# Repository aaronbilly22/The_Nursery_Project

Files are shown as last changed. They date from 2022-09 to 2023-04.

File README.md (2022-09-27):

# The Nursery Project

Developer Names: Aaron Billones, Juan Moncada, Gillian Ford, Steven Ramundi

Date of project start: September 21, 2022

The current method of preparing pots and trays to be filled with soil and populated with seeds at Sheridan Nurseries is a process with little to no automation, requiring many manual labour hours. Recently, the owners of these farms have been finding it increasingly more difficult to fill these roles with enough workers to run the operation smoothly, and meet production demands. We aim to aid in this process by designing and implementing a machine that is able to fill trays with pots and prepare them for populating with soil and seeds. This will alleviate the reliance on manual labour and improve the overall efficiency of the farm. 

The folders and files for this project are as follows:

docs - Documentation for the project\
refs - Reference material used for the project, including papers\
src - Source code\
test - Test cases\
parts - CAD/assembly and ordered parts

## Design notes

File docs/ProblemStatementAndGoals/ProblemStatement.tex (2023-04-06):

\documentclass{article}

\usepackage{tabularx}
\usepackage{booktabs}

\title{Problem Statement and Goals\\The Nursery Project}

\author{Aaron Billones, billonea\\Gillian Ford, fordg\\Juan Moncada, moncadaj\\Steven Ramundi, ramundis}

\date{September 26, 2022}

\input{../Comments}
\input{../Common}

\begin{document}

\maketitle

\begin{table}[hp]
\caption{Revision History} \label{TblRevisionHistory}
\begin{tabularx}{\textwidth}{llX}
\toprule
\textbf{Date} & \textbf{Developer(s)} & \textbf{Change}\\
\midrule
2022-09-25 & Juan Moncada,& Initial release\\&Aaron Billones,\\&Steven Ramundi,\\&Gillian Ford \\
2023-04-05 & Juan Moncada,& Updated to better reflect final product\\
\bottomrule
\end{tabularx}
\end{table}

\newpage

\section{Problem Statement}

Sheridan Nurseries is one of Canadas largest nursery opperations and is growing year by year.
In the past few years, the company has taken steps to automate their production line and streamline their operation.
A significant amount of manual labour was seen in between the delivery of skidded pots/trays and the beginning of the propagation 
assembly line. In the current state, one employee is used to recieve stacks of pots and trays from their respective skids,
populate the trays with pots, and feed the now filled trays into the assembly line where the propagation of plants into the pots begins.
This process currently requires full-time labour from at minimum one employee, if not more, to yield the required output.

\subsection{Problem}
Sheridan Nurseries currently has no automation in their process of populating their 
trays and pots thus needing significant manual labour.

\subsection{Inputs and Outputs}
\subsubsection{Physical Input}

Physical inputs will be stacks of trays and pots.
\subsubsection{Software Input}
The system will have a signal trigger to indicate if there are any trays and pots in order to carry out its operation. 
There will also be an on/off signal and safety kill switch.
\subsubsection{Physical Output}
The physical output of this project will be the trays filled with pots ready to move on to propagation.
\subsubsection{Software Output}
The systems will display a series of warnings such as load trays (when empty), load pots (when empty), 
and verification failed.

\subsection{Stakeholders}
The main stakeholders for this project will be the nursery manager, 
owner, and the individual(s) working the assembly line.

\subsection{Environment}
This project will be an even split between hardware and software as there is a need to build and incorporate into an existing assembly line.
Hardware will have to be used in order manipulate pots and trays, while software will be used to control said hardware 
aswel as take care of any verification that trays have been populated properly.
\section{Goals}
The main goal of this project is to develop a system for Sheridan Nurseries
that will replace the need for human workers in the current process of populating plant trays with pots. This will reduce the cost
of labour for the nursery, while being significantly less expensive than current alternatives. The goal of the system is to populate 
a standard tray with 1 pots in 30 seconds, equating to 2 trays per minute and 960 trays in an 8 hour shift. This is based on output 
numbers provided by the manager for the current system. Another goal for the project is to reload the trays and pots every 7.5 minutes.
This would require space for 15 trays and 150 pots.

\section{Stretch Goals}
The first stretch goal is to double the potential output of the machine. This will approximatley equate the output rate to maximum rate of the
machine responsible for populating pots with soil. The second stretch goal is to increase machine capacity to 60 trays and 600 pots to
maintain the goal of reloading the machine every 15 minutes. The third stretch goal is to make the machine capable of dealing with variable
tray and pot sizes.

\end{document}

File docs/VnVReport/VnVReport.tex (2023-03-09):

\documentclass[12pt, titlepage]{article}

\usepackage{booktabs}
\usepackage{tabularx}
\usepackage{longtable}
\usepackage{hyperref}
\hypersetup{
    colorlinks,
    citecolor=black,
    filecolor=black,
    linkcolor=red,
    urlcolor=blue
}
\usepackage[round]{natbib}

\input{../Comments}
\input{../Common}

\begin{document}

\title{Verification and Validation Report: The Nursery Project} 
\author{Aaron Billones, billonea\\Gillian Ford, fordg\\Juan Moncada, moncadaj\\Steven Ramundi, ramundis}
\date{March 8, 2023}
	
\maketitle

\pagenumbering{roman}

\section{Revision History}

\begin{tabularx}{\textwidth}{p{3cm}p{2cm}X}
\toprule {\bf Date} & {\bf Version} & {\bf Notes}\\
\midrule
2023-03-08 & 1.0 & Initial Revision\\

\bottomrule
\end{tabularx}

~\newpage

\section{Symbols, Abbreviations and Acronyms}

\renewcommand{\arraystretch}{1.2}
\begin{tabular}{l l} 
  \toprule		
  \textbf{symbol} & \textbf{description}\\
  \midrule 
  ART & Accessibility Requirements Test\\
CR & Conveyor Functional Requirement\\
CST & Conveyor Subsystem Test\\
EPET & Expected Physical Environment Test\\
LCD & Liquid-Crystal Display\\
LED & Light Emitting Diode\\
LRT & Learning Requirements Test\\
MG & Module Guide\\
MIS & Management Information Systems\\
NFR & Non-Functional Requirement\\
PDST & Pot Dispenser Subsystem Test\\
PDR & Pot Dispensing Functional Requirement\\
PCST & Pot-pulator Complete System Testing\\
PT & Precision Test\\
RT & Reliability Test\\
SCT & Safety Critical Test\\
SRS & Software Requirements Specification\\
SRT & Speed Requirements Test\\
TDST & Tray Dispenser Subsystem Test\\
TDR & Tray Dispensing Functional Requirement\\
VST & Verification Subsystem Test\\
VR & Verification Functional Requirement\\
  \bottomrule
\end{tabular}\\

\newpage

\tableofcontents

\listoftables %if appropriate

%\listoffigures %if appropriate

\newpage

\pagenumbering{arabic}

\section{Functional Requirements Evaluation}

\subsection{Pot-pulator Complete System Testing}

\begin{longtable}{ |p{0.12\textwidth}|*{4}{>{\centering\arraybackslash}p{0.20\textwidth}|}p{0.08\textwidth}|   }
  \caption{PCST Evaluation}
  \label{tab:PCST}\\
    \hline
    Test Number & Description & Input & Expected Output & Actual Output & Result\\
    \hline
    PCST-01 & Tray Dispenser Operation & Sensor reading of status of tray stack & Normal system operation & Normal system operation & Pass \\
    \hline
    PCST-02 & On Switch for Tray Dispenser Error & Pot-pulator switch set to on & Normal system operation & Normal system operation & Pass\\
    \hline
    PCST-03 & Pot Dispenser Operation & Sensor reading of status of pot stack & Normal system operation & Normal system operation & Pass\\
    \hline
    PCST-04 & On Switch for Pot Dispenser Error & Pot-pulator switch set to on & Normal system operation & Normal system operation & Pass\\
    \hline
    PCST-05 & Conveyor Operation & Tray placed on conveyor &  Normal system operation & Normal system operation & Pass\\
    \hline
    PCST-06 & Conveyor On Button & Pot-pulator switch set to on & Normal system operation & Normal system operation & Pass\\
    \hline
\end{longtable}

\subsection{Tray Dispenser Subsystem Testing}

\begin{longtable}{ |p{0.12\textwidth}|*{4}{>{\centering\arraybackslash}p{0.20\textwidth}|}p{0.08\textwidth}|  }
  \caption{TDST Evaluation}
  \label{tab:TDST}\\
    \hline
    Test Number & Description & Input & Expected Output & Actual Output & Result\\
    \hline
    TDST-01 & Tray Stack Detection & Sensor reads status of tray stack & Signal sent to microprocessor indicating trays are/are not present & Signal detected indicating presence of trays, no signal detected when trays are not present & Pass\\
    \hline
    TDST-02 & Operation from Tray Stack Detection & Sensor reads status of tray stack & Normal system operation & Normal system operation & Pass\\
    \hline
    TDST-03 & Tray from Stack to Conveyor & Stack of trays on tray dropper & One tray from stack is placed onto conveyor, next tray ready to be placed onto conveyor & One tray from stack is placed onto conveyor. Occasionally, two trays will be placed if there are only two remaining in the tray stack & Fail\\
    \hline
    TDST-04 & Verify Tray Status on Conveyor & Sensor reads status of tray on conveyor & Normal system operation & Tray dropper drops additional tray once first tray is no longer underneath tray dropper & Pass\\
    \hline
    
\end{longtable}

\subsection{Pot Dispenser Subsystem Testing}

\begin{longtable}{ |p{0.12\textwidth}|*{4}{>{\centering\arraybackslash}p{0.20\textwidth}|}p{0.08\textwidth}|  }
  \caption{PDST Evaluation}
  \label{tab:PDST}\\
    \hline
    Test Number & Description & Input & Expected Output & Actual Output & Result\\
    \hline
    PDST-01 & Pot from Stack to Tray & Simulated sensor input, two pot locations of tray directly below pot dispenser & Pot dispenser dispenses two pots into designated pot locations & Pot dispenser dispenses two pots, 70\% of cases tested saw pots dispensed into pot locations & Fail\\
    \hline
    PDST-02 & Tray Sensing & Trays placed in front of sensor & Signal sent to microprocessor indicating trays are/are not present & Signal detected indicating presence of trays, no signal detected when trays are not present & Pass\\
    \hline
    PDST-03 & Ability to Dispense 4" Diameter Pots & N/A & N/A & N/A & Pass\\
    \hline
    PDST-04 & Ability to Store/Dispense Multiple Pots & Ten pots, simulated sensor input & Pot dispenser dispenses two pots, reloads from stack, dispenses two pots, etc. until pot storage is empty & Pot dispenser dispenses two pots at a time for 5 cycles until all 10 pots are dispensed & Pass\\
    \hline
    PDST-05 & Pot Storage Detection & N/A & Signal output when no pots are detected in pot storage & Signal output when no pots are detected in pot storage & Pass\\
    \hline
    
\end{longtable}

\newpage

\subsection{Conveyor Subsystem Testing}

\begin{longtable}{ |p{0.12\textwidth}|*{4}{>{\centering\arraybackslash}p{0.20\textwidth}|}p{0.08\textwidth}|  }
  \caption{CST Evaluation}
  \label{tab:CST}\\
    \hline
    Test Number & Description & Input & Expected Output & Actual Output & Result\\
    \hline
    CST-01 & Conveyor Ability to Move Trays & Simulated inputs indicating conveyor can start & Constant speed of conveyor motor and belt & Constant speed of conveyor motor and belt & Pass\\
    \hline
    CST-02 & Conveyor Ability to Stop & Simulated signals from pot dispenser indicating tray is beneath pot dispenser & Conveyor motor and belt come to a stop & Conveyor motor and belt come to a stop & Pass\\
    \hline
    CST-03 & Conveyor Belt Friction & Mass of tray, tilt angle of conveyor belt & Maximum acceleration of conveyor belt & Maximum acceleration of conveyor belt & Pass\\
    \hline
    
\end{longtable}

\subsection{Verification Subsystem Testing}

\begin{longtable}{ |p{0.12\textwidth}|*{4}{>{\centering\arraybackslash}p{0.20\textwidth}|}p{0.08\textwidth}|  }
  \caption{VST Evaluation}
  \label{tab:VST}\\
    \hline
    Test Number & Description & Input & Expected Output & Actual Output & Result\\
    \hline
    VST-01 & Verify Correct Number of Pots in Tray & Tray filled with pots and tray not filled with pots & Signal sent indicating tray has not been completely filled with pots, no signal sent indicating all pot locations are filled & Signal sent indicating tray has not been completely filled with pots, no signal sent indicating all pot locations are filled & Pass\\
    \hline

\end{longtable}

\section{Nonfunctional Requirements Evaluation}

\subsection{Safety Critical Testing}

\begin{longtable}{ |p{0.12\textwidth}|*{4}{>{\centering\arraybackslash}p{0.20\textwidth}|}p{0.08\textwidth}|  }
  \caption{SCT Evaluation}
  \label{tab:SCT}\\
    \hline
    Test Number & Description & Input & Expected Output & Actual Output & Result\\
    \hline
    SCT-01 & Tray Dispenser Failure & Tray dispenser disconnect & System flags tray dispenser failure & System flags tray dispenser failure & Pass\\
    \hline
    SCT-02 & Pot Dispenser Failure & Pot dispenser disconnect & System flags pot dispenser failure & System flags pot dispenser failure & Pass\\
    \hline
    SCT-03 & Conveyor Failure & Conveyor disconnect & System flags conveyor failure & System flags conveyor failure & Pass\\
    \hline
    SCT-04 & Verification Failure & Verification disconnect & System flags verification failure & System flags verification failure & Pass\\
    \hline

\end{longtable}
		
\subsection{Precision Testing}

\begin{longtable}{ |p{0.12\textwidth}|*{4}{>{\centering\arraybackslash}p{0.20\textwidth}|}p{0.08\textwidth}|  }
  \caption{PT Evaluation}
  \label{tab:PT}\\
    \hline
    Test Number & Description & Input & Expected Output & Actual Output & Result\\
    \hline
    PT-01 & Tray Dispenser Precision & N/A & N/A & N/A & Pass\\
    \hline
    PT-02 & Pot Dispenser Precision & N/A & N/A & N/A & Pass\\
    \hline
    
\end{longtable}

\subsection{Reliability Testing}

\begin{longtable}{ |p{0.12\textwidth}|*{4}{>{\centering\arraybackslash}p{0.20\textwidth}|}p{0.08\textwidth}|  }
  \caption{RT Evaluation}
  \label{tab:RT}\\
    \hline
    Test Number & Description & Input & Expected Output & Actual Output & Result\\
    \hline
    RT-01 & Function Under Vibration & N/A & N/A & N/A & Pass\\
    \hline
    
\end{longtable}

\subsection{Expected Physical Environment Testing}

\begin{longtable}{ |p{0.12\textwidth}|*{4}{>{\centering\arraybackslash}p{0.20\textwidth}|}p{0.08\textwidth}|  }
  \caption{EPET Evaluation}
  \label{tab:EPET}\\
    \hline
    Test Number & Description & Input & Expected Output & Actual Output & Result\\
    \hline
    EPET-01 & Function Under Aerial Pollution & N/A & N/A & N/A & Pass\\
    \hline
    
\end{longtable}

\subsection{Speed Requirements Testing}

\begin{longtable}{ |p{0.12\textwidth}|*{4}{>{\centering\arraybackslash}p{0.20\textwidth}|}p{0.08\textwidth}|  }
  \caption{SRT Evaluation}
  \label{tab:SRT}\\
    \hline
    Test Number & Description & Input & Expected Output & Actual Output & Result\\
    \hline
    SRT-01 & Acceleration Displacement of Trays & N/A & N/A & N/A & Pass\\
    \hline
    SRT-02 & Pot Dispensing Rate & Stack of pots & Pots dispensed at desired rate & Pots dispensed at desired rate & Pass\\
    \hline
    SRT-03 & Tray Dispensing Rate & Stack of trays & Trays dispensed at desired rate & Trays dispensed at desired rate & Pass\\
    \hline

\end{longtable}

\subsection{Learning Requirements Testing}

\begin{longtable}{ |p{0.12\textwidth}|*{4}{>{\centering\arraybackslash}p{0.20\textwidth}|}p{0.08\textwidth}|  }
  \caption{LRT Evaluation}
  \label{tab:LRT}\\
    \hline
    Test Number & Description & Input & Expected Output & Actual Output & Result\\
    \hline
    LRT-01 & Operational Simplicity & N/A & N/A & N/A & Pass\\
    \hline

\end{longtable}

\subsection{Accessibility Testing}

\begin{longtable}{ |p{0.12\textwidth}|*{4}{>{\centering\arraybackslash}p{0.20\textwidth}|}p{0.08\textwidth}|  }
  \caption{ART Evaluation}
  \label{tab:ART}\\
    \hline
    Test Number & Description & Input & Expected Output & Actual Output & Result\\
    \hline
    ART-01 & Audio and Visual Indicators & Trigger signal & Corresponding light, sound, or screen display & Corresponding light, sound, or screen display & Pass\\
    \hline

\end{longtable}
	
\section{Comparison to Existing Implementation}	

After doing some research, there were some existing products that perform a similar 
function as the Pot-pulator. However, these products are large industrial machines that cost tens of thousands of dollars,
which is out of the price range for Sheridan Nurseries. Our goal was to develop a product that could perform the
the desired function of filling trays with pots at a inexpensive price point. The existing products are more robust and can operate
with larger loads within a given time frame. The Pot-pulator is intended to help solve Sheridan Nurseries' problem in an inexpensive
manner. We believe that we have achived this within a budget of only 750 dollars.

\section{Unit Testing}

  \subsection{Hardware Testing}
  The following section includes testing that was performed on critical hardware components
  of the system. These tests were performed for the purpose of verifying and understanding the  
  behaviour of each hardware component.
  \begin{enumerate}
  \item{HT-01: \textbf{AC Motor Control}}
  
  Test Description: The conveyor operates using an AC motor. In order to control it,
  a potentiometer and mechanical relay were used. The potentiometer controls the motor speed,
  and the relay controls on/off rotation of the motor.

  Input: Signal from Arduino to periodically switch the relay. Potentiometer position varies.

  Expected Output: Conveyor starts and stops based on the switching of relay. The speed of conveyor slows and speeds up
  in accordance to the potentiometer.

  Test Result: PASS
  \\
  \item{HT-02: \textbf{Stepper Motor Control}}\\
  Test Description: Many subsystems of the Pot-pulator uses stepper motors (ie. tray dispenser,pot dropper).
   Stepper drivers were wired and tested with step sizes that were offered by 
   the drivers purchased. 

  Input: Signals from Arduino to turn the motor 1 full revolution in full, half, quarter,
  eighth, and sixteenth stepping modes.

  Expected Output: 1 full revolution

  Test Result: PASS
  \\
  \item{HT-03: \textbf{Ultrasonic Range Finder Control}}\\
  Test Description: These sensors are used to meaure distances within the system for complete
  operation. Measurements were observed and verfied with a physical measuring tool (ie. ruler, tape measure)

  Input: Object placed in front of the sensor.

  Expected Output: Distance measured and displayed in the serial monitor (console).

  Test Result: PASS
\end{enumerate}

\section{Changes Due to Testing}

The changes due to testing are summarized below:
\\
\begin{enumerate}
  \item \textbf{Verification:}\\
  The bases of the verification mounts were recently expanded away from the
  conveyer by approximately 5 cm on either side, to address issues with the pots being too close to the 
  sensor when travelling down the conveyer, resulting in inaccurate readings.

  \item \textbf{Pot Dropper:}\\
  The part design of the threaded discs that drop the pots needed to be modified.
  After the inital testing of the pot dropper, the design resulted in pots being dropped
  in groups larger than 1. During each rotation of the stepper motors that are intended to drop 1 pot
  at a time, often times more than 1 pot would be dropped. Because of these results, the part design was 
  changed and tested. The part design underwent multiple design changes in order to have the highest success rate 
  when dropping pots.

  \item \textbf{Tray Dispenser:}\\
  The part design of the toothed cylinder which is responsible for dispensing the trays on to the conveyor
  was changed during testing. The diameter and number of teeth dictate whether or not the trays will drop one at a time with 
  each motor increment. Several models were designed and tested until a design with diameter of approximately 5cm with 12 teeth was found to be the 
  most effective model.
\end{enumerate}
		
\section{Trace to Requirements}

The following table outlines all of the system tests and how they relate to the
relevent requirements. The requirements can be referenced in the SRS document.\\

\begin{longtable}{ |p{4cm}|p{8cm}|  }
  \caption{Corresponding Test IDs and Requirements}
  \label{tab:Table1}\\
  
  \hline
  \textbf{Test ID} & \textbf{Supporting Requirements}\\
  \hline
  TDST-01 &  TDR3, TDR5\\
  \hline
  TDST-02 &  TDR4, TDR5 \\
  \hline
  TDST-03 &  TDR2 \\
  \hline
  TDST-04 &  TDR2 \\
  \hline
  PDST-01 &  PDR2 \\
  \hline
  PDST-02 &  PDR2 \\
  \hline
  PDST-03 &  PDR3 \\
  \hline
  PDST-04 &  PDR4 \\
  \hline
  PDST-05 &  PDR5, PDR6 \\
  \hline
  PCST-01 &  TDR1 \\
  \hline
  PCST-02 &  TDR5, TDR6 \\
  \hline
  PCST-03 &  TDR7 \\
  \hline
  PCST-04 &  PDR1 \\
  \hline
  PCST-05 &  PDR6, PDR7 \\
  \hline
  PCST-06 &  PDR8 \\
  \hline
  VST-01 &  VR1 \\
  \hline
  VST-02&  VR2 \\
  \hline
  SCT-01 &  NFR12 \\
  \hline
  SCT-02 &  NFR12 \\
  \hline
  SCT-03 &  NFR12 \\
  \hline
  SCT-04 &  NFR12 \\
  \hline
  PT-01 & NFR13 \\
  \hline
  PT-02 & NFR14 \\
  \hline
  RT-01 & NFR17 \\
  \hline
  EPET-01 & NFR20 \\
  \hline
  LRT-01&  NFR6 \\
  \hline
  ART-01 & NFR7 \\
  \hline
  SRT-01 & NFR8 \\
  \hline
  SRT-02 & NFR9 \\
  \hline
  SRT-03 & NFR10 \\
  \hline
\end{longtable}

\newpage

\section{Trace to Modules}	

The following table outlines all of the system tests and how they relate to the
relevent modules. The modules can be referenced in the MG document.\\

\begin{longtable}{ |p{4cm}|p{8cm}|  }
  \caption{Corresponding Test IDs and Modules}
  \label{tab:Table1}\\
  
  \hline
  \textbf{Test ID} & \textbf{Supporting Modules}\\
  \hline
  TDST-01 &  M9\\
  \hline
  TDST-02 &  M9 \\
  \hline
  TDST-03 &  M10 \\
  \hline
  TDST-04 &   M10\\
  \hline
  PDST-01 &  M4 \\
  \hline
  PDST-02 &  M4 \\
  \hline
  PDST-03 &  M5 \\
  \hline
  PDST-04 &  M3 \\
  \hline
  PDST-05 & M6 \\
  \hline
  PCST-01 &  M9 \\
  \hline
  PCST-02 & M12 \\
  \hline
  PCST-03 &  M6 \\
  \hline
  PCST-04 &  M3 \\
  \hline
  PCST-05 & M3 \\
  \hline
  PCST-06 &  M7 \\
  \hline
  VST-01 &  M13 \\
  \hline
  VST-02&  M14 \\
  \hline
  SCT-01 &  M12 \\
  \hline
  SCT-02 &  M6 \\
  \hline
  SCT-03 &  M8 \\
  \hline
  SCT-04 &  M14 \\
  \hline
  PT-01 & M12 \\
  \hline
  PT-02 & M6 \\
  \hline
  SRT-01 & M12 \\
  \hline
  SRT-02 & M6 \\
  \hline
  SRT-03 & M12 \\
  \hline
\end{longtable}

\newpage

\bibliographystyle{plainnat}
\bibliography{../../refs/References}

\newpage{}
\section*{Appendix --- Reflection}

The information in this section will be used to evaluate the team members on the
graduate attribute of Lifelong Learning.  Please answer the following questions:
\begin{enumerate}
  \item
In what ways was the Verification and Validation (VnV) Plan different
from the activities that were actually conducted for VnV? If there were
differences, what changes required the modification in the plan? Why
did these changes occur? Would you be able to anticipate these changes
in future projects? If there weren’t any differences, how was your team
able to clearly predict a feasible amount of effort and the right tasks
needed to build the evidence that demonstrates the required quality?
(It is expected that most teams will have had to deviate from their
original VnV Plan.)

The VnV Plan differed slightly from the activities conducted for VnV. This was
mainly due to design changes in our product. Primarily, the changes made to the 
mechanism responsible for placing trays onto the conveyor belt changed the way 
testing was done for this mechanism. Originally, trays were meant to be placed 
on the floor, adjacent to the conveyor belt, rather than directly above the conveyor
belt as they are now. The implementation and design proposed for the original plan
required more components, and thus, required more testing to be done. The design changes
made to this component yielded less tests to establish its function, as well as changing 
the behaviour of the system as a whole. Specifically, our previous design required a reset 
button to be manually pressed by an operator to notify the system when stock was replenished, 
meaning this feature would have to be tested to ensure all aspects of the system were reset 
after a restock. Since the current design operates based on a rolling stock, and the sequence 
of the assembly is based entirely on the readings of multiple sensors, a manual reset was no 
longer required, and all tests involving this feature were not viable. In future projects, we 
can ensure that the design of our respective projects is finalized before creating a VnV Plan, 
thereby allowing us to follow the VnV Plan when conducting VnV activities.
\end{enumerate}

\end{document}

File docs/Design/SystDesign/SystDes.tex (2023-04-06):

\documentclass[12pt, titlepage]{article}

\usepackage{fullpage}
\usepackage[round]{natbib}
\usepackage{multirow}
\usepackage{booktabs}
\usepackage{tabularx}
\usepackage{graphicx}
\graphicspath{ {./images/} }
\usepackage{float}
\usepackage{hyperref}
\hypersetup{
    colorlinks,
    citecolor=blue,
    filecolor=black,
    linkcolor=red,
    urlcolor=blue
}

\input{../../Comments}
\input{../../Common}

\newcounter{acnum}
\newcommand{\actheacnum}{AC\theacnum}
\newcommand{\acref}[1]{AC\ref{#1}}

\newcounter{ucnum}
\newcommand{\uctheucnum}{UC\theucnum}
\newcommand{\uref}[1]{UC\ref{#1}}

\newcounter{mnum}
\newcommand{\mthemnum}{M\themnum}
\newcommand{\mref}[1]{M\refbottomrule{#1}}

\begin{document}

\title{System Design for Pot-pulator} 
\author{Team \#24, The Nursery Project\\Aaron Billones, billonea\\Gillian Ford, fordg\\Juan Moncada, moncadaj\\Steven Ramundi, ramundis}
\date{January 18, 2023}

\maketitle

\pagenumbering{roman}

\section{Revision History}

\begin{tabularx}{\textwidth}{p{3cm}p{4cm}X}
  \toprule {\bf Date} & {\bf Version} & {\bf Notes}\\
  \midrule
  2023-01-18 & Juan Moncada,& Initial release\\&Aaron Billones,\\&Steven Ramundi,\\&Gillian Ford \\
  2023-04-05 & Aaron Billones, &Update for final documentation\\ &Steven Ramundi\\
  \bottomrule
  \end{tabularx}

\newpage

\section{Reference Material}

This section records information for easy reference.

\subsection{Abbreviations and Acronyms}

\renewcommand{\arraystretch}{1.2}
\begin{tabular}{l l} 
  \toprule		
  \textbf{symbol} & \textbf{description}\\
  \midrule 
  CR & Conveyor Functional Requirement\\
  NFR & Non-Functional Requirement\\
  PDR & Pot Dispensing Functional Requirement\\
  SRS & Software Requirements Specification\\
  TDR & Tray Dispensing Functional Requirement\\
  VR & Verification Functional Requirement\\
  MIS & Module Interface Specification \\
  MG & Module Guide \\
  LED & Light-Emitting Diode\\
  CAD & Computer-Aided Design\\
  LCD & Liquid Crystal Display\\
  \bottomrule
\end{tabular}\\

\newpage

\tableofcontents

\newpage

\listoftables

\listoffigures

\newpage

\pagenumbering{arabic}

\section{Introduction}

The Pot-pulator is a machine with purpose of aiding Sheridan Nurseries in 
populating their trays with pots, in order to prepare them for filling with 
soil and seeds.\\\\Their current method of populating the trays with pots is a 
process with little to no automation, requiring many manual hours of labour. 
Each year, 250,000 annual plants need to be produced by the nursery. Recently, 
the supervisors have found it increasingly more difficult to fill positions with 
enough workers to run the operation smoothly and meet production demand. 
The Pot-pulator will alleviate the large reliance on manual labour and 
improve the overall efficiency of the nursery. \\\\This document consists of a 
detailed design overview of the Pot-pulator. The system overview, system 
variables, user interfaces, hardware design and electrical design will be 
presented in this document.

\section{Purpose}

This document describes the overall system functionality and the design overview 
of the Pot-pulator. It will describe how the mechanical, electrical, and software 
components will interact with each other, and the various design decisions made 
within the system. The Module Guide (MG) and Module Interface Specification (MIS) 
are additional design documents that provide a further in depth design of the 
components in each module of the system.

\section{Scope}
The following figure shows the boundary between the Pot-pulator device and its functionality
within the given environment.

\begin{figure}[H]
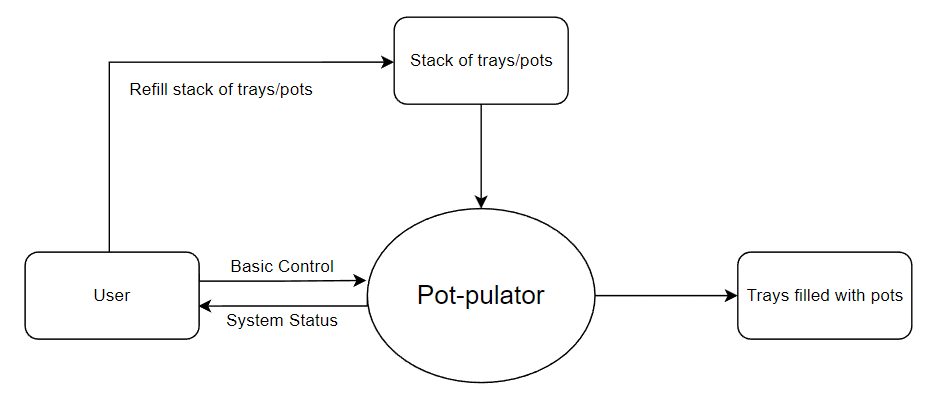
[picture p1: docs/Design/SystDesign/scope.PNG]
  
  \caption{System Context Diagram}
  \label{fig:scope}
\end{figure}

\section{Project Overview}

\subsection{Normal Behaviour}

The Pot-pulator needs to be filled with empty pots and trays by the user. Upon pressing the "start" button,
the Pot-pulator begins its operation with no further interaction required by the user.
Under normal operation, the ideal behaviour of the Pot-pulator will be as follows:
\begin{enumerate}
  \item User fills the machine with empty pots and trays
  \item User flips the power switch on
  \item User flips the conveyor switch on and the conveyor begins to move forward
  \item A tray will automatically drop down and begin moving along the conveyor
  \item The tray will hit 2 lever switches which lines up the tray to prepare for pot dispensing
  \item Stop the conveyor when pots are lined up with the next row on the tray and dispense 2 pots at a time in the tray
  \item Continue moving the conveyor to the next available pair of slots in the tray
  \item Repeat steps 6 and 7 until the entire tray is filled with pots (10 pots)
  \item Once the tray is filled with pots, the verification subsystem determines if all the pots have been placed correctly in the tray
\end{enumerate}

\noindent Throughout the opreation of the device, the user interface displays the current status of the machine.

\subsection{Undesired Event Handling}
The Pot-pulator is vulnerable to many undesired events during operation. The user will be notified should anything
go wrong with the system via the user interface and LEDs.
\subsubsection{Pot/Tray Misalignement}
A very common issue that could arise with the Pot-pulator is that there is the possibility
of a pot not being placed correctly in the tray due to misalignement. To mitigate this risk,
the verification subsystem was implemented to ensure that there are pots in all of the tray slots.
If there are missing pots, the user will be notified and the tray may be removed from the conveyor by hand.

\subsubsection{Motor Jam/Malfunction}
If a motor is unable to turn or fails, the system comes to a stop and the user is notfied about the issue.
The user is then expected to remove the object that is blocking the motor from moving. If the motor refuses to turn even without obstruction,
the motor will most likely need to be replaced by a qualified individual.

\subsection{Component Diagram}
\begin{figure}[H]
  \centering
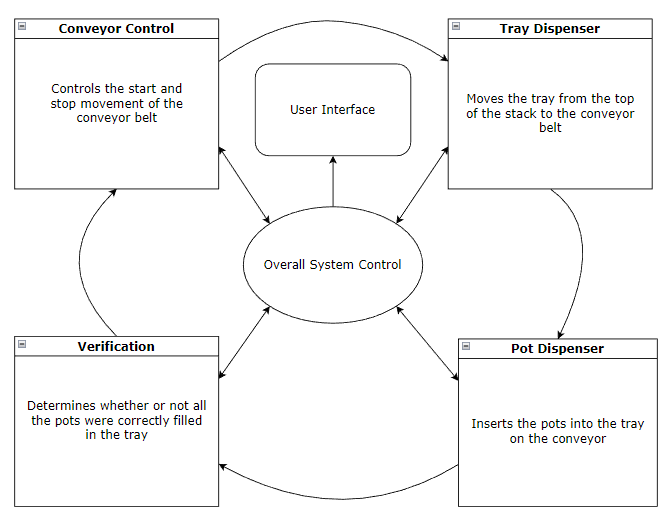
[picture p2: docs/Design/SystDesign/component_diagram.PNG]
  
  \caption{Component Diagram}
  \label{fig:componentdiagram}
\end{figure}
\subsection{Connection Between Requirements and Design} \label{SecConnection}

  The table below shows the traceability between design components and requirements specified in the SRS.
  
\begin{table}[H]
\caption{Requirements and System Design}
\begin{tabularx}{\textwidth}{|l|X|}
\hline
\textbf{Component} & \textbf{Corresponding Requirement} \\ \hline
Overall System Control  & NFR11, NFR12 \\ \hline
Conveyor Control   & CR1, CR2, CR3, CR4, CR5, CR6, NFR8 \\ \hline
Tray Dispenser   & TDR1, TDR2, TDR3, TDR4, TDR5, TDR6, TDR7, NFR4, NFR10, NFR13, NFR16 \\ \hline
Pot Dispenser   &  PDR1, PDR2, PDR3, PDR4, PDR5, PDR6, PDR7, PDR8, NFR4, NFR9, NFR14, NFR15  \\ \hline
Verification   &  VR1, VR2, NFR5 \\ \hline
User Interface  &  NFR7 \\ \hline
\end{tabularx}
\end{table}

\section{System Variables}

\subsection{Monitored Variables}
\begin{table}[H]
\caption{Monitored Variables}
\begin{tabular}{ |p{3cm}|p{9cm}|p{2cm}|p{1cm}| }
  \hline
  Variable & Description & Type & Units\\
  \hline
  Sensor Distances & Measured distances that the sensor identifies
   & Distance & mm\\
  \hline
  System State & Determines the state of the system (ie. Ready, Running, Error, Success)
   & State &  N/A\\
  \hline
 \end{tabular}\\\\
 \end{table}

\subsection{Controlled Variables}
\begin{table}[H]
\caption{Controlled Variables}
\begin{tabular}{ |p{3cm}|p{9cm}|p{2cm}|p{1cm}| }
  \hline
  Variable & Description & Type & Units\\
  \hline
  Motor Speeds & The speeds at which the motors in the system will turn
   & Speed & rad/s\\
  \hline
  Voltage In & Voltage going into the system
   & Voltage & V\\
  \hline
  Current In & Current going into the system
   & Current &  A\\
  \hline
  LEDs & LED status lights
   & Boolean & N/A\\
  
  \hline
 \end{tabular}\\\\
\end{table}

\subsection{Constants Variables}
\begin{table}[H]
  \caption{Constants Variables}
\begin{tabular}{ |p{3cm}|p{8.9cm}|p{2.1cm}|p{1cm}| }
  \hline
  Variable & Description & Type & Units\\
  \hline
  Motor Acceleration & The acceleration at which the motors in the system will turn
   & Acceleration & rad/s\textsuperscript{2}\\
  \hline
  Pots Dispensed & Pots dispensed by the system per cycle
   & Quantity & pots per cycle\\
  \hline
  Trays Dispensed & Trays dispensed by the system per cycle
   & Quantity &  trays per cycle\\
  \hline
  Total Distance & Total distance travelled by trays
   & Distance & m\\
  
  \hline
 \end{tabular}\\\\
\end{table}

\section{User Interfaces}

The User Interface will consist of a set of status messages to allow the operator to safely 
interact with the machine. It will also consist of visual signals to alert
the operator of any action required (e.g. tray/pot restock, verification error, etc.).
See Appendix A for interface layout concept.

\section{Design of Hardware}

\subsection{Pot Dropper}

The pot dropper subsystem is comprised of:
\begin{itemize}
  \item 1 Arduino Uno microcontroller
  \item 4 stepper motors (Nema-17)
  \item 4 stepper motor drivers (A4988)
  \item 2 servo motors (SG92R)
  \item 2 custom servo motor attachments
  \item 1 custom servo mount
  \item 1 custom servo/sensor mount
  \item 4 custom pot dropper discs
  \item 1 ultrasonic range finder (HC-SR04)
  \item 2 lever switches
  \item screws and bracket mounts
  \item aluminum t-slotted extrusion
\end{itemize}
The pot dropper is fabricated with aluminum framing to support the mechanism. The stepper
 motors are attached to the frame, and the pot dropper discs are attached to the shaft 
of the stepper motors. The lever switches are attached to the servo motors via the servo motor attachments, and are 
mounted to the aluminum extrusion via the servo motor mounts. See Appendix B.1 for a CAD diagram of the pot dropper screw.

\subsection{Tray Dropper}

The tray dropper subsystem is comprised of:
\begin{itemize}
  \item 1 Arduino Uno microcontroller
  \item 2 stepper motors (Nema-17)
  \item 2 stepper motor drivers (A4988)
  \item 2 custom tray dispenser gears
  \item 1 ultrasonic range finder (HC-SR04)
  \item 1 custom sensor mount
  \item 2 D-slotted steel shaft and connectors
  \item screws and bracket mounts
  \item aluminum t-slotted extrusion
\end{itemize}
The tray dropper is fabricated with aluminum framing to support the mechanism. The 
stepper motors and shaft connectors are attached to the framing, and the shafts 
are secured to the shaft connectors. The ultrasonic range finder is mounted to the 
extrusion via the sensor mount. See Appendix B.2 for a CAD diagram of the tray dropper assembly 
and a CAD diagram of the tray dropper gear.

\subsection{Conveyor Belt}

The conveyor belt used for the Pot-pulator is a 58 x 29.5 x 11.5 inch conveyor with a 50W AC motor driven by a custom printed
circuit board. Additional hardware components includes:
\begin{itemize}
  \item 1 Arduino Uno microcontroller
  \item 2 ultrasonic range finders (HC-SR04)
  \item 1 mechanical relay (SDR-05VDC-SL-C)
  \item 1 potentiometer
\end{itemize}

\subsection{Verification}

The verification subsystem is comprised of:
\begin{itemize}
  \item 2 ultrasonic range finders (HC-SR04)
  \item 2 custom sensor mounts
\end{itemize}
The ultrasonic range finders are mounted to the conveyor via the sensor mounts.

\subsection{User Interface}

The user interface is comprised of:
\begin{itemize}
  \item 1 Arduino Uno microcontroller
  \item 3.5 inch TFT 320x480 LCD (HXD8357D)
\end{itemize}

\section{Design of Electrical Components}

The Pot-pulator has a number of electrical components in the system. A complete overview of the circuit diagram
can be found in section C of the appendix. To improve modularity and for easier troubleshooting,
the electrical components were divided in to 4 subsystems based on the control of the system: conveyor control/verification, pot
dispensing, tray dispensing, and user interface. These subsystems are each controlled using an 
Arduino Uno while communicating with each other when necessary. For each subsystem,
its respective Arduino reads inputs from electronic components such as sensors, switches, and buttons and 
outputs control accordingly to the various motors. The Arduinos from each of the 
subsystems send a status bit to the LCD subsystem. If an error were to occur in
one of the subsystems, the LCD will show the appropriate status message and the entire system will act accordingly.

% \section{Design of Communication Protocols}

% \wss{If appropriate}

\section{Timeline}

\begin{table}[H]
  \caption{Timeline}
\begin{tabular}{ |p{3cm}|p{5cm}|p{4cm}|p{2cm}| }
  \hline
  Task & Description & Team Member(s) & Deadline\\
  \hline
  Pot Dropper Design & Design of pot dropper hardware and software
  & Juan Moncada and Gillian Ford & Juanuary 23, 2023\\
  \hline
  Tray Dropper Design & Design of tray dropper hardware and software
  & Steven Ramundi and Aaron Billones & January 23, 2023\\
  \hline
  Pot Dropper Fabrication & Fabrication of pot dropper frame and apparatus
  & Juan Moncada & January 31, 2023\\
  \hline
  Tray Dropper Fabrication & Fabrication of tray dropper and elevator frame and apparatus
  & Steven Ramundi and Aaron Billones & January 31, 2023\\
  \hline
  Verification Fabrication & Fabrication of verification System
  & Gillian Ford & January 31, 2023\\
  \hline
  Electrical Fabrication & Fabrication and assembly of all electrical components
  & All members & February 2, 2023\\
  \hline
  Testing & Testing of all subsystems and components
  & All members & February 6, 2023\\
  \hline

\end{tabular}
\end{table}

% \bibliographystyle {plainnat}
% \bibliography{../../../refs/References}

\newpage{}

\appendix

\section{Interface}

% \wss{Include additional information related to the appearance of, and
% interaction with, the user interface}
\begin{figure}[H]
  \centering
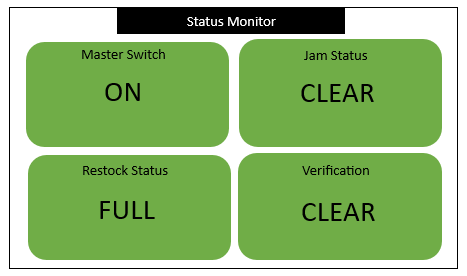
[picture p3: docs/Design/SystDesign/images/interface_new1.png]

\caption{Example of Interface}
  \label{fig:interface1}
\end{figure}
The above figure shows the user interface during normal operation. No errors are being displayed.

\begin{figure}[H]
  \centering
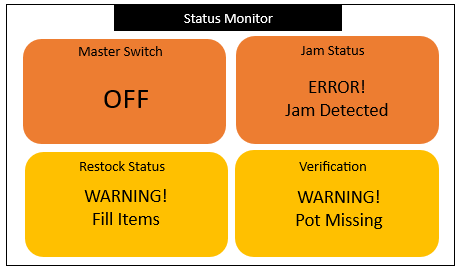
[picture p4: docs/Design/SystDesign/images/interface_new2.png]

\caption{Example of Interface}
  \label{fig:interface2}
\end{figure}
\noindent The above figure shows the user interface while all errors are present and the Pot-pulator is off. 

\section{Mechanical Hardware}

\subsection{Pot Dropper}
\begin{figure}[H]
  \centering
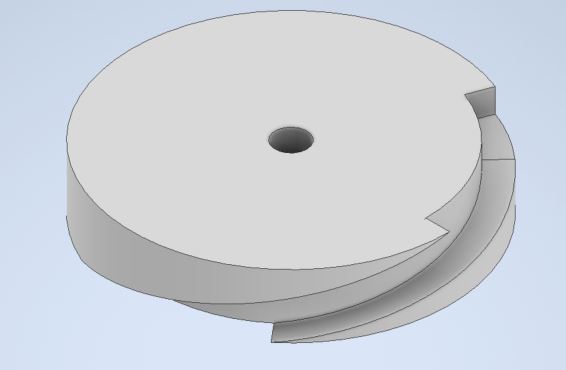
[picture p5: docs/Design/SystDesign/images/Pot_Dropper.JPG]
  
  \caption{Pot Dropper Screw}
  \label{fig:potdropper1}
\end{figure}

\subsection{Tray Dropper}
\begin{figure}[H]
  \centering
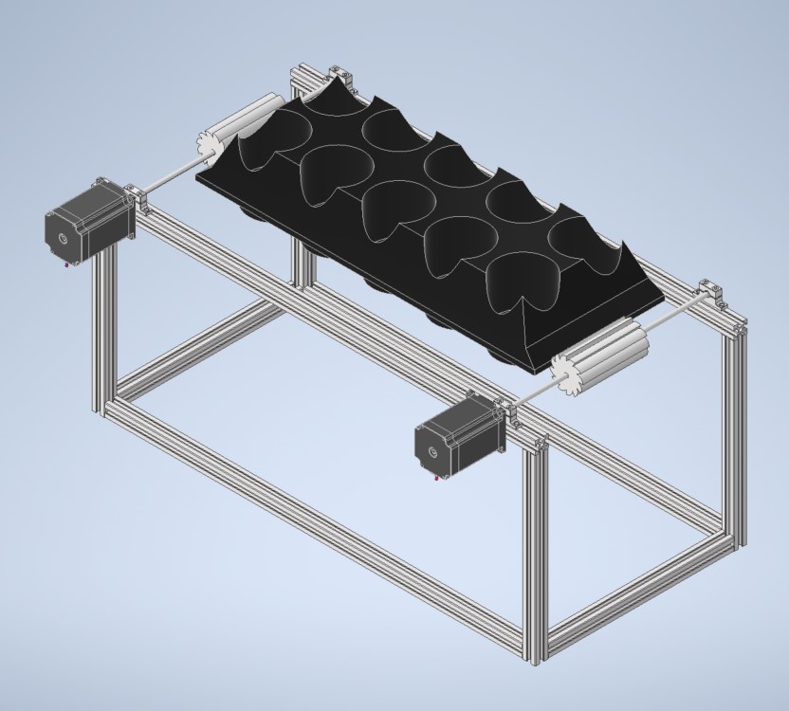
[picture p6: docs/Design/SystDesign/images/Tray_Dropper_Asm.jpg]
  
  \caption{Tray Dropper Assembly}
  \label{fig:traydropper1}
\end{figure}

\begin{figure}[H]
  \centering
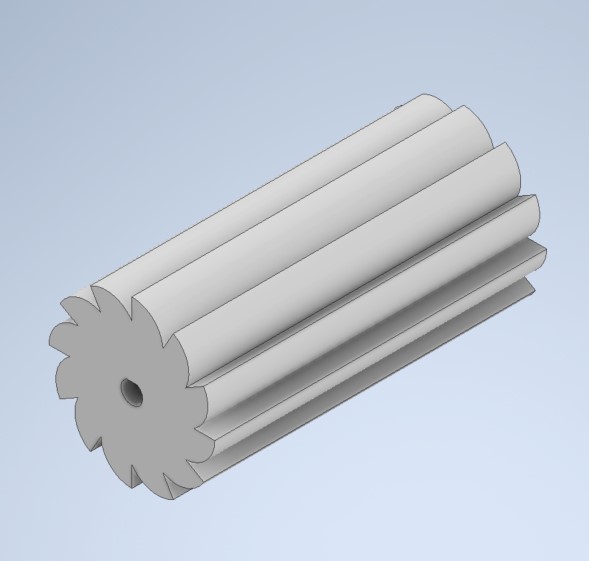
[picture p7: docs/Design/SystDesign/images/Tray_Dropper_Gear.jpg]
  
  \caption{Tray Dropper Gear}
  \label{fig:traydropper2}
\end{figure}

\section{Electrical Components}

\begin{figure}[H]
  \centering
  
  \caption{Circuit Diagram}
  \label{fig:circuit}
\end{figure}

\section{Reflection}

The information in this section will be used to evaluate the team members on the
graduate attribute of Problem Analysis and Design.  Please answer the following questions:

\begin{enumerate}
  \item What are the limitations of your solution?  Put another way, given
  unlimited resources, what could you do to make the project better?\\

  One limitation of our solution would be the overall load capacity of the system.
  We are constrained by the space where the pots and trays are being stored in the device
  that makes it difficult to upsize. Another limitation of our solution is that there are only
  a set number of speeds we can make the conveyor move at relative to the number of relays we use.
  This is because we used the existing AC motor that came with the conveyor and its control board rather than
  designing a control board from scratch. We still wanted to control the AC motor with an Arduino in some way with digital signals.
  This created some issues in controlling the motor to an exact speed we wanted. Given unlimited resources,
  we would ideally get a conveyor system that had a DC motor and could seemlessly be controlled using 
  digital signals. We would also create more robust mounts and obtain more accurate sensors in order to mitigate risks
  during operation.

  \item Give a brief overview of other design solutions you considered.  What
  are the benefits and tradeoffs of those other designs compared with the chosen
  design?  From all the potential options, why did you select documented design?\\
  
  We considered a number of design solutions on each subsystem of our device. For controlling the AC motor (conveyor),
  we considered purchasing a digital potentiometer. This option would give us more precise control over the motor, 
  but was much more expensive that using relays. Another design option we considered was using a pully system to lift the 
  trays into position in preparation for dispensing. We opted out of this option because the pully system would be less accurate and reliable
  than our rack and pinion design. We considered dispensing the trays in a simiar way to the pots using a threaded dropping system. However,
  given the shape and flexibility of the trays, we determined that this would be a unreliable way of getting the trays on the conveyor. The 
  gantry method of moving the tray is much more reliable.
\end{enumerate}

\end{document}

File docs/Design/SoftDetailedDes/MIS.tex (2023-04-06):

\documentclass[12pt, titlepage]{article}

\usepackage{amsmath, mathtools}

\usepackage[round]{natbib}
\usepackage{amsfonts}
\usepackage{amssymb}
\usepackage{graphicx}
\usepackage{colortbl}
\usepackage{xr}
\usepackage{hyperref}
\usepackage{longtable}
\usepackage{xfrac}
\usepackage{tabularx}
\usepackage{float}
\usepackage{siunitx}
\usepackage{booktabs}
\usepackage{multirow}
\usepackage[section]{placeins}
\usepackage{caption}
\usepackage{fullpage}

\hypersetup{
bookmarks=true,     % show bookmarks bar?
colorlinks=true,       % false: boxed links; true: colored links
linkcolor=red,          % color of internal links (change box color with linkbordercolor)
citecolor=blue,      % color of links to bibliography
filecolor=magenta,  % color of file links
urlcolor=cyan          % color of external links
}

\usepackage{array}

\externaldocument{../../SRS/SRS}

\input{../../Comments}
\input{../../Common}

\begin{document}

\title{Module Interface Specification for Pot-pulator}

\author{Team \#24, The Nursery Project\\Aaron Billones, billonea\\Gillian Ford, fordg\\Juan Moncada, moncadaj\\Steven Ramundi, ramundis}
\date{January 18, 2023}

\maketitle

\pagenumbering{roman}

\section{Revision History}

\begin{tabularx}{\textwidth}{p{3cm}p{4cm}X}
  \toprule {\bf Date} & {\bf Contributors} & {\bf Notes}\\
  \midrule
  2023-01-18 & Juan Moncada,& Initial release\\&Aaron Billones,\\&Steven Ramundi,\\&Gillian Ford \\
  2023-04-05 & Steven Ramundi, & Updated for final documentation\\&Aaron Billones\\
  \bottomrule
  \end{tabularx}

~\newpage

\section{Symbols, Abbreviations and Acronyms}

See SRS Documentation at \url{https://github.com/aaronbilly22/The\_Nursery\_Project/blob/main/docs/SRS/SRS.pdf}

\newpage

\tableofcontents

\newpage

\pagenumbering{arabic}

\section{Introduction}

The following document details the Module Interface Specifications for
The Nursery Project.

\noindent Complementary documents include the System Requirement Specifications
and Module Guide.  The full documentation and implementation can be
found at \url{https://github.com/aaronbilly22/The\_Nursery\_Project/blob/main/docs/SRS/SRS.pdf}. 

\section{Notation}

The structure of the MIS for modules comes from \citet{HoffmanAndStrooper1995},
with the addition that template modules have been adapted from
\cite{GhezziEtAl2003}.  The mathematical notation comes from Chapter 3 of
\citet{HoffmanAndStrooper1995}.  For instance, the symbol := is used for a
multiple assignment statement and conditional rules follow the form $(c\_1
\Rightarrow r\_1 | c\_2 \Rightarrow r\_2 | ... | c\_n \Rightarrow r\_n )$.

The following table summarizes the primitive data types used by Pot-pulator. 

\begin{center}
\renewcommand{\arraystretch}{1.2}
\noindent 
\begin{tabular}{l l p{7.5cm}} 
\toprule 
\textbf{Data Type} & \textbf{Notation} & \textbf{Description}\\ 
\midrule
character & char & a single symbol or digit\\
integer & $\mathbb{Z}$ & a number without a fractional component in (-$\infty$, $\infty$) \\
natural number & $\mathbb{N}$ & a number without a fractional component in [1, $\infty$) \\
real & $\mathbb{R}$ & any number in (-$\infty$, $\infty$)\\
\bottomrule
\end{tabular} 
\end{center}

\noindent
% The specification of \progname \ uses some derived data types: sequences, strings, and
% tuples. Sequences are lists filled with elements of the same data type. Strings
% are sequences of characters. Tuples contain a list of values, potentially of
% different types. In addition, \progname \ uses functions, which
% are defined by the data types of their inputs and outputs. Local functions are
% described by giving their type signature followed by their specification.

\section{Module Decomposition}

The following table is taken directly from the Module Guide document for this project.

\begin{table}[h!]
  \centering
  \begin{tabular}{p{0.3\textwidth} p{0.6\textwidth}}
  \toprule
  \textbf{Level 1} & \textbf{Level 2}\\
  \midrule
  
  {Hardware-Hiding Module} & ~ \\
  \midrule
  
  \multirow{7}{0.3\textwidth}{Behaviour-Hiding Module}
  & Pot Dropping Input Module \\
  & Pot Dropping Stepper Module\\
  & Pot Dropping Output Module\\
  & Conveyor Input Module\\
  & Conveyor Movement Module\\
  & Tray Dispenser Input Module\\ 
  & Tray Dispenser Output Module \\
  & Verification Output Module \\
  
  \midrule
  
  \multirow{3}{0.3\textwidth}{Software Decision Module}
  & Pot dropping Position Module\\
  & Verifications Analysis Module\\
  & Communication Module\\
  & Front End Module\\
  \bottomrule
  
  \end{tabular}
  \caption{Module Hierarchy}
  \label{TblMH}
  \end{table}

\newpage
~\newpage

\section{MIS of Pot Dropping Input Module} \label{potdroppingInput} 

\subsection{Pot Dropping Input}

\subsection{Uses}
Pot Dropping Position Module (M4)\\

\subsection{Syntax}
\subsubsection{Exported Constants}
trigPin: ultrasonic range finder trigger pin\\
echoPin: ultrasonic range finder echo pin\\
LIMIT\_SWITCH\_PIN\_L: left servo limit switch pin\\
LIMIT\_SWITCH\_PIN\_R: right servo limit switch pin\\
\subsubsection{Exported Access Programs}

% \begin{center}
% \begin{tabular}{p{2cm} p{4cm} p{4cm} p{2cm}}
% \hline
% \textbf{Name} & \textbf{In} & \textbf{Out} & \textbf{Exceptions} \\
% \hline
% \wss{accessProg} & - & - & - \\
% \hline
% \end{tabular}
% \end{center}
N/A

\subsection{Semantics}

\subsubsection{State Variables}

duration := float\\
distance := float\\

\subsubsection{Environment Variables}

trigPin: output pin sending signal to ultrasonc range finder\\
echoPin: input pin receiving signal from ultrasonc range finder\\
LIMIT\_SWITCH\_PIN\_L: input pin receiving signal from arm switch attached to servo\\
LIMIT\_SWITCH\_PIN\_R: input pin receiving signal from arm switch attached to servo\\
Servo Servo1: servo object of servo motor 1\\
Servo Servo2: servo object of servo motor 2\\
\subsubsection{Assumptions}

N/A

\subsubsection{Access Routine Semantics}

% \noindent \wss{accessProg}():
% \begin{itemize}
% \item transition: \wss{if appropriate} 
% \item output: \wss{if appropriate} 
% \item exception: \wss{if appropriate} 
% \end{itemize}
N/A

\subsubsection{Local Functions}

loop, setup

\section{MIS of Pot Dropping Stepper Module} \label{potdroppingstepper} 

\subsection{Pot Dropping Stepper}

\subsection{Uses}
Pot Dropping Output Module (M6) 

\subsection{Syntax}

\subsubsection{Exported Constants}
const int stepPin1: step pin of stepper 1\\
const int dirPin1: direction pin of stepper 1\\
const int stepPin2: step pin of stepper 2\\
const int dirPin2: direction pin of stepper 2\\
\subsubsection{Exported Access Programs}
N/A

\subsection{Semantics}

\subsubsection{State Variables}

N/A

\subsubsection{Environment Variables}

const int stepPin1: output pin sending signal to stepper 1\\
const int dirPin1: output pin sending signal to stepper 1\\
const int stepPin2: output pin sending signal to stepper 2\\
const int dirPin2: output pin sending signal to stepper 2\\
\subsubsection{Assumptions}

N/A

\subsubsection{Access Routine Semantics}

N/A

\subsubsection{Local Functions}

N/A

\section{MIS of Pot Dropping Output Module} \label{potdroppingOutput} 

\subsection{Pot Dropping Output}

\subsection{Uses}
Communication (section \ref{communication})

\subsection{Syntax}
\subsubsection{Exported Constants}
servoPin 1: servo 1 command pin\\
servoPin 2: servo2 command pin\\
errorPin: user interface error pin\\
conveyorPin: conveyor control pin\\
\subsubsection{Exported Access Programs}

N/A

\subsection{Semantics}
\subsubsection{State Variables}

N/A

\subsubsection{Environment Variables}

servoPin 1: output pin sending signal to servo 1\\
servoPin 2: output pin sending signal to servo 2\\
errorPin: output pin sending error signal to front-end\\
conveyorPin: output pin sneding stop/start signal to conveyor\\

\subsubsection{Assumptions}

N/A

\subsubsection{Access Routine Semantics}

N/A

\subsubsection{Local Functions}

N/A

\section{MIS of Conveyor Input Module} \label{conveyorInput} 

\subsection{Conveyor Input}

\subsection{Uses}
Conveyor Movement \ref{conveyorMovement}

\subsection{Syntax}
\subsubsection{Exported Constants}
const int stopPin: stop pin to conveyor\\
\subsubsection{Exported Access Programs}

N/A

\subsection{Semantics}

\subsubsection{State Variables}

N/A

\subsubsection{Environment Variables}

const int stopPin: input pin receiving signal from pot dropper to stop/start conveyor movement\\

\subsubsection{Assumptions}

N/A
\subsubsection{Access Routine Semantics}

N/A
\subsubsection{Local Functions}

N/A

\section{MIS of Conveyor Movement Module} \label{conveyorMovement}

\subsection{Conveyor Movement}

\subsection{Uses}
Communication \ref{communication}

\subsection{Syntax}

\subsubsection{Exported Constants}
const int relayPin: relay pin from conveyor\\
\subsubsection{Exported Access Programs}

N/A

\subsection{Semantics}

\subsubsection{State Variables}

N/A

\subsubsection{Environment Variables}

const int relayPin: output pin sending stop/start signal to conveyor relay\\

\subsubsection{Assumptions}

N/A

\subsubsection{Access Routine Semantics}

N/A

\subsubsection{Local Functions}

N/A

\section{MIS of Tray Dispenser Input Module} \label{trayDispenserInput} 

\subsection{Tray Dispenser Input}

\subsection{Uses}
Tray Dispenser Output \ref{trayDispenserOutput}

\subsection{Syntax}

\subsubsection{Exported Constants}
const int trigPin: ultrasonic range finder trigger pin\\
const int echoPin: ultrasonic range finder echo pin\\
\subsubsection{Exported Access Programs}

N/A

\subsection{Semantics}

\subsubsection{State Variables}

distance := int\\
duration := long\\
\subsubsection{Environment Variables}

const int trigPin: output pin sending signal to ultrasonc range finder\\
const int echoPin: input pin receiving signal from ultrasonc range finder\\

\subsubsection{Assumptions}

N/A

\subsubsection{Access Routine Semantics}

N/A

\subsubsection{Local Functions}

GetDistance(): returns distance as read from ultrasonic range finder
\section{MIS of Tray Dispenser Output Module} \label{trayDispenserOutput} 

\subsection{Tray Dispenser Output}

\subsection{Uses}
Communication \ref{communication}

\subsection{Syntax}

\subsubsection{Exported Constants}
const int ms1: stepping mode\\
const int ms2: stepping mode\\
const int ms3: stepping mode\\
cosnt int stepPin: step pin of stepper motors\\
const int dirPin: direction pin of stepper motors\\
\subsubsection{Exported Access Programs}

N/A

\subsection{Semantics}

\subsubsection{State Variables}

N/A

\subsubsection{Environment Variables}

const int ms1: output pin to set stepping mode\\
const int ms2: output pin to set stepping mode\\
const int ms3: output pin to set stepping mode\\
cosnt int stepPin: output pin sending signal to stepper motors\\
const int dirPin: output pin sending signal to stepper motors\\

\subsubsection{Assumptions}

N/A

\subsubsection{Access Routine Semantics}

N/A

\subsubsection{Local Functions}

N/A
\section{MIS of Verification Output Module} \label{verificationOutput} 

\subsection{Verification Output}

\subsection{Uses}
Communication \ref{communication}

\subsection{Syntax}

\subsubsection{Exported Constants}
const int LED\_PIN: pin to LED and front-end\\

\subsubsection{Exported Access Programs}

N/A

\subsection{Semantics}

\subsubsection{State Variables}

N/A

\subsubsection{Environment Variables}

const int LED\_PIN: output pin to LED and front-end to signify failure in verification\\

\subsubsection{Assumptions}

N/A
\subsubsection{Access Routine Semantics}

N/A

\subsubsection{Local Functions}

N/A

\section{MIS of Pot Dropping Position Module} \label{potDroppingPosition} 

\subsection{Pot Dropping Position}

\subsection{Uses}
Pot Dropping Stepper \ref{potdroppingstepper}

\subsection{Syntax}

\subsubsection{Exported Constants}

LIMIT\_SWITCH\_PIN\_L: left servo limit switch pin\\
LIMIT\_SWTCH\_PIN\_R: right servo limit switch pin\\

\subsubsection{Exported Access Programs}

N/A

\subsection{Semantics}

\subsubsection{State Variables}

distance := float
\subsubsection{Environment Variables}

LIMIT\_SWITCH\_PIN\_L: input pin to determine if tray has made contact with left limit switch\\
LIMIT\_SWTCH\_PIN\_R: input pin to determine if tray has made contact with right limit switch\\

\subsubsection{Assumptions}

N/A

\subsubsection{Access Routine Semantics}

N/A

\subsubsection{Local Functions}

N/A

\section{MIS of Verification Analysis Module} \label{verificationAnalysis} 

\subsection{Module}

\subsection{Uses}

Verification Output \ref{verificationOutput}
\subsection{Syntax}

\subsubsection{Exported Constants}
const int TRIG\_PIN: ultrasonic range finder trigger pin\\
cosnt int ECHO\_PIN: ultrasonic range finder echo pin\\
const int TRIG\_PIN2: ultrasonic range finder trigger pin\\
cosnt int ECHO\_PIN2: ultrasonic range finder echo pin\\
\subsubsection{Exported Access Programs}

N/A

\subsection{Semantics}

\subsubsection{State Variables}

duration\_us := float\\
distance\_cm := float\\
duration2\_us := float\\
distance2\_cm := float\\

\subsubsection{Environment Variables}

const int TRIG\_PIN: output pin to ultrasonic range finder\\
cosnt int ECHO\_PIN: input pin from ultrasonic range finder\\
const int TRIG\_PIN2: output pin to ultrasonic range finder\\
cosnt int ECHO\_PIN2: input pin from ultrasonic range finder\\

\subsubsection{Assumptions}

N/A

\subsubsection{Access Routine Semantics}

N/A

\subsubsection{Local Functions}

N/A
\section{MIS of Communication Module} \label{communication}

\subsection{Communication}

\subsection{Uses}

N/A
\subsection{Syntax}

\subsubsection{Exported Constants}
N/A
\subsubsection{Exported Access Programs}

N/A

\subsection{Semantics}

\subsubsection{State Variables}

N/A

\subsubsection{Environment Variables}

N/A

\subsubsection{Assumptions}

N/A

\subsubsection{Access Routine Semantics}

N/A

\subsubsection{Local Functions}

N/A

\section{MIS of Front End Module} \label{fronEnd} 

\subsection{Front End}

\subsection{Uses}
Communication \ref{communication}

\subsection{Syntax}

\subsubsection{Exported Constants}
LCD\_CS: chip select pin\\
LCD\_CD: command/data pin\\
LCD\_WR: write pin\\
LCD\_RD: read pin\\
LCD\_RESET: reset pin\\
\subsubsection{Exported Access Programs}

N/A

\subsection{Semantics}

\subsubsection{State Variables}

status\[\] := byte\\
state\[\] := byte\\
oldstate\[\] := byte\\

\subsubsection{Environment Variables}

LCD\_CS: chip select pin\\
LCD\_CD: command/data pin\\
LCD\_WR: write pin\\
LCD\_RD: read pin\\
LCD\_RESET: reset pin\\

\subsubsection{Assumptions}

N/A

\subsubsection{Access Routine Semantics}

masterSwitchON(): writes master switch on status to display\\
masterSwitchOFF(): write master switch off status to display\\
verification() writes verification clear to display\\
verifcationDetected(): writes verification error to display\\
trayJam(): writes tray jam status warning to display\\
trayStock(): writes tray stock status clear to display\\
potJam(): writes pot jam status warning to display\\
potStock(): write pot stock status warning to display\\

\subsubsection{Local Functions}

N/A

\newpage

\bibliographystyle {plainnat}
\bibliography {../../../refs/References}

\newpage

\end{document}

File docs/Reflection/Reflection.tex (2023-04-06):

\documentclass{article}

\usepackage{tabularx}
\usepackage{booktabs}

\title{Reflection Report on Pot-pulator}
\title{Reflection Report on Pot-pulator}

\author{Team \#24, The Nursery Project\\Aaron Billones, billonea\\Gillian Ford, fordg\\Juan Moncada, moncadaj\\Steven Ramundi, ramundis}
\date{April 5, 2023}

\input{../Comments}
\input{../Common}

\begin{document}

\maketitle

% \plt{Reflection is an important component of getting the full benefits from a
% learning experience.  Besides the intrinsic benefits of reflection, this
% document will be used to help the TAs grade how well your team responded to
% feedback.  In addition, several CEAB (Canadian Engineering Accreditation Board)
% Learning Outcomes (LOs) will be assessed based on your reflections.}

\section{Changes in Response to Feedback}

% \plt{Summarize the changes made over the course of the project in response to
% feedback from TAs, the instructor, teammates, other teams, the project
% supervisor (if present), and from user testers.}

% \plt{For those teams with an external supervisor, please highlight how the feedback 
% from the supervisor shaped your project.  In particular, you should highlight the 
% supervisor's response to your Rev 0 demonstration to them.}

\subsection{SRS and Hazard Analysis}

Changes were made to SRS based on feedback from teammates, the instructor, and TAs. 
Requirements were adjusted as the design and scope of the project changed.

\subsection{Design and Design Documentation}

Design underwent many major changes throughout the process based on feedback. Between Proof of Concept 
and Rev0 Demo, feedback from teammates influenced a major change in the final design of the tray dropper 
subsystem. After Rev0, feeback from the instructor and TA influenced the revised design of the pot dropper 
subsystem, increasing the accuracy of the machine overall.

\subsection{VnV Plan and Report}

The VnV Plan and Report changed based on feedback from peers. Testing plans were updated to better ensure all 
components of the machine were being tested thoroughly, and all edge cases were considered when conducting testing.
\section{Design Iteration (LO11)}

The design process of the Pot-pulator went through various iterations.
Our initial design for inserting the pots into the trays consisted of 
actuators that would place the pots inside the slots. While this solution 
is more precise and robust than our final solution, it requires very expensive
materials in order to have it fully operational. After confirming our design for dispensing the pots,
there were iterations with our 3-D printed parts that improved with each iteration.
At first the thread in the disc was too wide where the device would drop multiple pots at one time.
Therefore, we went through several design iterations in order to achieve the correct part design.\\\\

\noindent Similar to the pot dispenser, the tray dispenser design had been through multiple iterations.
Initially, we were going to use and gantry system to move the trays from a stack to the conveyor belt.
We soon came to realize that this solution would also be very expensive and lacking the time/materials in 
order to obtain a working final solution. After we iterated through our gear design which drops the trays
from a stack above the conveyor one at a time. This also took some iterating as we needed to ensure that only one tray 
would be dropped when we want it to.

\section{Design Decisions (LO12)}

With our project being more of a physical solution rather than a software one, 
there were many assumptions made and a lot more constraints pressed upon us.
For example, the 750 dollar budget limited us to changing some of our designs because some initial ones were too expensive.
Some assumptions made were that the area would be clean and weather would not affect our device.
Weather proofing our device would cost more money and materials that we did not have access to.
We also should have made more timely design decisions as there were many instances where we were falling behind.
More timely design goals should have been set which would help our overall design process and success in the project.

\section{Economic Considerations (LO23)}

% \plt{Is there a market for your product? What would be involved in marketing your 
% product? What is your estimate of the cost to produce a version that you could 
% sell?  What would you charge for your product?  How many units would you have to 
% sell to make money? If your product isn't something that would be sold, like an 
% open source project, how would you go about attracting users?  How many potential 
% users currently exist?}

We believe there is a market for our product. All Sheridan Nurseries farms are ran in the same way 
as the farm which we used to influence our design. The cost of the manual labour does not justify the 
purchase of the machines that are currently available on the market, but our low cost solution is perfect 
for Sheridan Nurseries' current situation. It is also a great solution for any industrial potting farm which 
owns a soil and seed filling machine, but does not own a pot and tray sorting machine. Marketing the product 
would involve giving live demonstrations to decision makers at the farms or distributing videos showcasing the functionality 
of the machine and highlighting the value it will provide. We estimate it would cost approximately \$700 to manufacture 
if our current sourcing methods are used, but this price can be drastically reduced if it were to be manufactured in large 
quantities. We would charge a price which would translate to a 60\% markup. At a cost of \$700, this would mean setting the price 
at approximately \$1150. We would be making about \$450 per machine, and our break even point would be dependent on the amount of 
capital we would be required to invest to establish a manufacturing process, and the amount of fixed costs that would incur on other 
activities such as advertising.

\section{Reflection on Project Management (LO24)}

% \plt{This question focuses on processes and tools used for project management.}

\subsection{How Does Your Project Management Compare to Your Development Plan}

% \plt{Did you follow your Development plan, with respect to the team meeting plan, 
% team communication plan, team member roles and workflow plan.  Did you use the 
% technology you planned on using?}

The project resembled the structure outlined in the development plan well. meetings were set, updates were given regularly, and each member was held accountable for their contributions to the project, this has a direct correlation with setting reasonable goals in the development plan and not shooting for the moon with meetings and objectives.

\subsection{What Went Well?}

% \plt{What went well for your project management in terms of processes and 
% technology?}

Overall, the design and integration of the capstone went well, dividing the project into subsections when surprisingly well and each member being responsible for their subsection with standardized communication made integration run smoothly.

\subsection{What Went Wrong?}

% \plt{What went wrong in terms of processes and technology?}

A consideration that was overlooked at the beginning of the project was the amount of impact that precision would have on the project, while sections and parts were designed to be as accurate as possible, the designs relied on perfect alignment and sometimes ideal situations, these where not accounted for in the design.

\subsection{What Would you Do Differently Next Time?}

% \plt{What will you do differently for your next project?}

If we had the opportunity to go back and change our project we would focus much more on developing a more redundant machine that relied less on accuracy and precision. We would also set smaller goals and set aside more time to integrate separate subsystems and tuning.

\end{document}

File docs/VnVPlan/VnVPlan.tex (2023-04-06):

\documentclass[12pt, titlepage]{article}

\usepackage{booktabs}
\usepackage{tabularx}
\usepackage{hyperref}
\usepackage{longtable}
\usepackage{array}
\hypersetup{
    colorlinks,
    citecolor=blue,
    filecolor=black,
    linkcolor=red,
    urlcolor=blue
}
\usepackage[round]{natbib}

\input{../Comments}
\input{../Common}

\begin{document}

\title{Project Title: System Verification and Validation Plan for The Nursery Project} 
\author{Aaron Billones, billonea\\Gillian Ford, fordg\\Juan Moncada, moncadaj\\Steven Ramundi, ramundis}

\date{November 2, 2022}

\maketitle
\thispagestyle{empty}

\pagenumbering{roman}

\begin{tabularx}{\textwidth}{p{3cm}p{4cm}X}
    \toprule {\bf Date} & {\bf Contributors} & {\bf Notes}\\
    \midrule
    2022-11-02 & Juan Moncada,& Initial release\\&Aaron Billones,\\&Steven Ramundi,\\&Gillian Ford \\
    2023-03-08 & Steven Ramundi & Updated to reflect changes made during testing\\
    \bottomrule
\end{tabularx}

\newpage

\tableofcontents

\listoftables

\newpage

\section{Symbols, Abbreviations and Acronyms}

% \renewcommand{\arraystretch}{1.2}
\begin{longtable}{ p{4cm}p{8cm}  }
  \toprule		
  \textbf{symbol} & \textbf{description}\\
  \midrule 
  CR & Conveyor Functional Requirement\\
  NFR & Non-Functional Requirement\\
  PDR & Pot Dispensing Functional Requirement\\
  TDR & Tray Dispensing Functional Requirement\\
  VR & Verification Functional Requirement\\
  SRS & Software Requirements Specification\\
  PCST & Pot-pulator Complete System Testing\\
  TDST & Tray Dispenser Subsystem Test\\
  PDST & Pot Dispenser Subsystem Test\\
  CST & Conveyor Subsystem Test\\
  VST & Verification Subsystem Test\\
  SCT & Safety Critical Test\\
  PT & Precision Test\\
  RT & Reliability Test\\
  EPET & Expected Physical Environment Test\\
  LED & Light Emitting Diode\\
  LCD & Liquid-Crystal Display\\
  SRT & Speed Requirements Test\\
  ART & Accessibility Requirements Test\\
  LRT & Learning Requirements Test\\
  MIS & Management Information Systems\\
 MG & Module Guide\\

  \bottomrule
\\
\caption{Acronyms}
\label{tab:title}
\end{longtable}

\newpage

\pagenumbering{arabic}

\section{General Information}

This document is the Verification \& Validation Plan of the Pot-pulator. This machine will be built for Sheridan Nurseries, filling trays with pots, preparing them to be populated with soil and seeds, to reduce the manual labour of the workers at the farm. The Verification \& Validation Plan will consider the testing of each part of the Pot-pulator, including the respective tray and pot droppers, the sensor verification section, and the conveyor belt. 

\subsection{Summary}
The testing of the software in this report will be with C++ and Python. These will be used to perform specific tasks based on groups of related written statements. Testing with these types of software will involve specific testing involving multiple functions. 

\subsection{Objectives}
The main objective of this report is to build confidence in the software used for the Pot-pulator. This is preparation for any errors in testing, so there is an opportunity to come up with solutions. When every possible error is worked through in advance, it increases the likelihood of the project’s success. 

\subsection{Relevant Documentation}
Reports referenced or corresponding to this plan include the Pot-pulator’s SRS, Development Plan, MIS and MG. 
\section{Plan}
The following section will outline the plan for system testing. The testing 
will be divided into 5 categories; the 4 separate subsystems that make up the system and the system.

\subsection{Verification and Validation Team}

The testing will be distributed evenly amongst the members of the team. The interdisciplinary aspect of this 
project means that certain members focused more on certain parts of the capstone, thus verification will be 
done evenly but there will be an emphasis on testing sections in which each member was not a major contributing partner.
The following table shows the main point of focus of each group member and their area of focus on the project.
\begin{center}
  \begin{tabular}{ |l|l|l| } 
    \hline
    \textbf{Team member} & \textbf{Area of Focus } & \textbf{Verification Area of Focus} \\ 
    \hline
    Gillian Ford   & Pot dropping and Verification & Conveyor and tray dispensing \\
    Aaron Billones & Conveyor and tray dispensing & Pot dropping and Verification \\
    Steven Ramundi & Conveyor and tray dispensing & Pot dropping and Verification \\
    Juan Moncada   & Pot dropping and Verification & Conveyor and tray dispensing\\
    \hline
  \end{tabular}
\end{center}

\subsection{Milestones}
The following are milestones for the corresponding testing including the date of expected completion. 
\begin{center}
  \begin{tabular}{ |l|l| } 
    \hline
    \textbf{Testing} & \textbf{expected date of completion } \\ 
    \hline
    Pot dropping Subsystem    & December 5th 2022 \\
    Tray dispensing Subsystem & December 5th 2022 \\
    Conveyor Subsystem        & December 5th 2022 \\
    Verification Subsystem    & January 10th 2023 \\
    Whole System              & January 21th 2023 \\

    \hline
  \end{tabular}
\end{center}

\subsection{SRS Verification Plan}

The design verification plan will be comprised of the verification of 4 of the core subsystems.
 Each of these subsystems will be tested individually to include all possible scenarios, once 
 individual testing has been completed the system will be put together and tested as a whole.\\

The verification of system will take place alongside the end user. Sheridan Nurseries has been
 scheduled to have an early look at the unfinished system so that all functional and non-functional 
 requirements may be looked over and made sure to be fulfilled. This process will also allow for the 
 foundations of new requirements that could be added before the final build of the system. There will 
 also be multiple review sessions including by group members and peers. Peer review setions will be
 to happen after every milestone has been reached\\

The review will go over the following checklist to make sure that the system is meeting all functional 
and non-functional requirement. The following is the SRS validation checklist.

\begin{center}
  \begin{tabular}{ |m{10cm}|m{3cm}| } 
    \hline
    \textbf{Requirement Validate} & \textbf{Pass or fail } \\ 
    \hline
    System interface should be clear, legible, and obvious. & \\
    Subsystems are communicating with integration board.  & \\
    System is running smoothly, without the presence or audible or visual errors.& \\
    There are no lose or exposed wires or electronics.& \\
    There are no expose gears, chains or moving parts.& \\
    
    \hline
  \end{tabular}
\end{center}

\subsection{Design Verification Plan}
Each of the subsystem will be tested individually. The following section will outline the individual testing
for each individual testing subsystem. The following are the design validation checklists for the 
further development of the project will warrant the addition to the following checklist. Checklist will be updated as new items are brought up.

 \subsubsection{Conveyor}
 \begin{center}
  \begin{tabular}{ |m{10cm}|m{3cm}| } 
    \hline
    \textbf{Requirement Validate} & \textbf{Pass or fail } \\ 
    \hline
    Conveyor is stable so that movements from subsystems do not cause any vibration, tipping or other unwanted movement. & \\

    \hline
  \end{tabular}
\end{center}

\subsubsection{Tray Dispenser}
\begin{center}
 \begin{tabular}{ |m{10cm}|m{3.2cm}| } 
   \hline
   \textbf{Requirement Validate} & \textbf{Pass or fail } \\ 
   \hline
   Tray dispenser runs smoothly and is not translating any unwanted motion into the system. & \\

   \hline
 \end{tabular}
\end{center}

\subsubsection{Pot Dispenser}
\begin{center}
 \begin{tabular}{ |m{10cm}|m{3cm}| } 
   \hline
   \textbf{Requirement Validate} & \textbf{Pass or fail } \\ 
   \hline
   pot dispenser runs smoothly and is not translating any unwanted motion into the system. & \\
  
   \hline
 \end{tabular}
\end{center}

\subsubsection{Verification}
\begin{center}
 \begin{tabular}{ |m{10cm}|m{3cm}| } 
   \hline
   \textbf{Requirement Validate} & \textbf{Pass or fail } \\ 
   \hline
    Verification is able to display distinct subsystem failures& \\
    verification operates consistently and is able to identify initiation and operation failures distinctly & \\

   \hline
 \end{tabular}
\end{center}

\subsection{Verification and Validation Plan Verification Plan}
As the project progresses there will be the requirement to add, remove or alter verification and 
Validation steps/procedures. In order to capture this as the system progresses in its completion 
when major verification and validation milestones are hit, they will be accompanied with the
review of the verification and validation plan. This review will trigger any updates that will
need to be put through.

\subsection{Implementation Verification Plan}
Implementation verification will take place through code walkthroughs. these will take place between
 members of the same subsystem focus. When there is a code to be uploaded and implemented into the system,
  the member which created the code will go through a in depth walk through with the other member working
   on the same subsystem. This is done for two main reasons. The first, all members of the same subsystem 
   focus will have in depth knowledge of all of the code that that subsystem has implemented into the system.
    Second, the code will be checked by a member who is of equal knowledge of the subsystem, its 
    characteristics and requirements thus makeing inspection of the code more fruitful.

\subsection{Automated Testing and Verification Tools}

Automated testing will take plae through the use of a linter, most specifically the Python
PEP 8 linter per the development plan. The code will be ran through the pep 8 linter before
any milestone to emphasize the use of the most condensed and verified code before milestones.
this was eluded to in the development plan for this project.

\section{System Test Description}
	
\subsection{Tests for Functional Requirements}

The following section includes system test cases for functional requirements.
The tests are designed in such a way to ensure that all the functional requirements are met.
For reference of the functional requirements, please review the SRS document.

\begin{enumerate}

\subsubsection{Pot-pulator Complete System Testing}

\item{PCST-01: \textbf{Tray Dispenser Operation}}

Control: Manual

Initial State: Some amount of trays in the stack.

Input: Sensor reads the status of tray stack.

Output: System operates or displays an error and stops all system operation. 

Test Case Derivation: If the tray dispenser is empty or malfunctions, the system will output an error on a screen (tray dispenser malfunction/empty). If this error occurs, it will stop all sections of the machine. Otherwise, operate normally. 

How test will be performed: Trays will be removed from the stack, then trays will be put in the stack. Operation and results on the screen will be observed.  
\\
\item{PCST-02: \textbf{On Switch for Tray Dispenser Error}}

Control: Manual

Initial State: Some number of trays in the stack, pot-pulator switch is set to off.

Input: Pot-pulator switch is set to on.

Output: System operates or remains idle and displays an error. 

Test Case Derivation: If the tray dispenser is empty or malfunctions, the system will output an error on a screen (tray dispenser malfunction/empty). If this error occurs, the machine will not start. Otherwise, operate normally. 

How test will be performed: Trays will be removed from the stack, then trays will be put in the stack. Operation and results on the screen will be observed.  
\\
% \item{PCST-03: \textbf{Tray Dispenser Reset}}

% Control: Manual

% Initial State: Some number of trays in the stack, an error is displayed on the screen.

% Input: Pot-pulator reset button is pressed.

% Output: System operates or remains idle and displays an error. 

% Test Case Derivation: When there is a malfunction, the reset button will be pressed. If the malfunction is not solved, the system will output an error on the screen (tray dispenser malfunction/empty). Otherwise, system will start again normally. 

% How test will be performed: Reset button will be pressed during an error. Operation and results on the screen will be observed.  
% \\
\item{PCST-03: \textbf{Pot Despenser Operation }}
Control: Manual

Initial State: Some amount of pots in the stack.

Input: Sensor reads the status of pot stack.

Output: System operates or displays an error and stops all system operation. 

Test Case Derivation: If the pot dispenser is empty or malfunctions, the system will output an error on a screen (pot dispenser malfunction/empty). If this error occurs, it will stop all sections of the machine. Otherwise, operate normally. 

How test will be performed: Pots will be removed from the stack, then trays will be put in the stack. Operation and results on the screen will be observed.  
\\
\item {PCST-04: \textbf{On Switch for Pot Dispenser Error}}

Control: Manual

Initial State: Some number of pots in the stack, pot-pulator switch is set to off.

Input: Pot-pulator switch is set to on.

Output: System operates or remains idle and displays an error. 

Test Case Derivation: If the pot dispenser is empty or malfunctions, the system will output an error on a screen (pot dispenser malfunction/empty). If this error occurs, the machine will not start. Otherwise, operate normally. 

How test will be performed: pots will be removed from the stack, then pots will be put in the stack. Operation and results on the screen will be observed.  
\\
% \item {PCST-06: \textbf{Pot Dispenser Reset}}

% Control: Manual

% Initial State: Some number of pots in the stack, an error is displayed on the screen.

% Input: Pot-pulator reset button is pressed.

% Output: System operates or remains idle and displays an error. 

% Test Case Derivation: When there is a malfunction, the reset button will be pressed. If the malfunction is not solved, the system will output an error on the screen (pot dispenser malfunction/empty). Otherwise, system will start again normally. 

% How test will be performed: Reset button will be pressed during an error. Operation and results on the screen will be observed.  
% \\
\item {PCST-05: \textbf{Conveyer Operation }}

Control: Manual

Initial State: Tray put on conveyor.

Input: Sensor reads the status of tray on conveyor.

Output: System operates or displays an error and stops all the system operation. 

Test Case Derivation: If a component of the conveyer malfunctions, the system will output an error on a screen (conveyer malfunction). If this error occurs, it will stop all sections of the machine. Otherwise, operate normally. 

How test will be performed: Trays will be fed onto the conveyor correctly, then trays will be placed stuck on purpose. Operation and results on the screen will be observed. 
\\
\item {PCST-06: \textbf{Conveyer On Button }}

Control: Manual

Initial State: Some trays are put on conveyer, switch is set to off.

Input: Pot-pulator switch is set to on.

Output: System operates or remains idle and displays an error. 

Test Case Derivation: If the conveyer malfunctions, the system will output an error on a screen (conveyer malfunction) If this error occurs, the machine will not start. Otherwise, operate normally. 

How test will be performed: Trays will be placed on the conveyer in incorrect positions, then in correct positions. Operation and results on the screen will be observed.  
\\
% \item {PCST-09: \textbf{Conveyer Reset}}

% Control: Manual

% Initial State: Some trays are put on conveyer, switch is set to off.

% Input: Pot-pulator switch is set to on.

% Output: System operates or remains idle and displays an error. 

% Test Case Derivation: When there is a malfunction, the reset button will be pressed. If the malfunction is not solved, the system will output an error on the screen (conveyer malfunction Otherwise, system will start again normally. 

% How test will be performed: Reset button will be pressed during an error. Operation and results on the screen will be observed.

\subsubsection{Tray Dispenser Subsystem Testing}
        
  \item{TDST-01: \textbf{Tray Stack Detection}}
  
  Control: Static, Manual
            
  Initial State: No trays present in the stack. Trays present in the stack.
            
  Input: Sensor reads the status of tray stack.
            
  Output: Sends a signal/bit to microprocessor that tells the system there are/aren't trays present.

  Test Case Derivation: The observed signal/bit is the expected value. The subsystem does not operate when no trays are present.
  
  How test will be performed: All other sensors and subsystems will be switched off. 
  All trays will be removed from the stack. The detection bit will be observed. 
  Then trays will be placed in the stack, and the detection bit will be observed.
\\
  \item{TDST-02: \textbf{Operation from Tray Stack Detection}}
  
  Control: Dynamic, Manual
            
  Initial State: Some amount of trays in the stack.
            
  Input: Sensor reads the status of tray stack.
            
  Output: Subsystem operates or remains idle.
  
  Test Case Derivation: If no trays are present, the subsystem will not operate 
  and remain ready in the idle state. Otherwise, operate normally.
  
  How test will be performed: All other sensors and subsystems will be switched off. 
  Trays will be removed from the stack and operation will be observed. Trays will be 
  put in the stack and operation will be observed.\\

  \item{TDST-03: \textbf{Tray from Stack to Conveyor}}
  
  Control: Dynamic, Manual
            
  Initial State: There is a stack of trays beside the vacant conveyor with the subsystem in idle position.
            
  Input: Stack of trays.
            
  Output: One tray from the stack is placed onto the end of the conveyor and returns to idle position.
  
  Test Case Derivation: There is a tray in the correct designated position.
  The subsystem moves into the ready idle state to retrieve more trays.
            
  How test will be performed: All other sensors and subsystems will be switched off. 
  The system will be manually activated to retrieve one tray from its stack.
  The success or failure will be observed.
\\
  \item{TDST-04: \textbf{Verify Tray Status on Conveyor}}
  
  Control: Dynamic, Manual
            
  Initial State: Tray put on conveyor.
            
  Input: Sensor reads the status of tray on conveyor.
            
  Output: Subsystem continues operation or stops.
  
  Test Case Derivation: Subsystem continues operation (when successful) or stops (when tray is stuck/fails to move on conveyor).
  
  How test will be performed: Trays will be fed onto the conveyor correctly. Results will be observed.
  then trays will be placed stuck on purpose. Results will be observed.
  
  \end{enumerate}

\subsubsection{Pot Dispenser Subsystem Testing}

\begin{enumerate}
 
  \item{PDST-01: \textbf{Pot from Stack to Tray}}
  
  Control: Dynamic, Manual
            
  Initial State: Pot dispenser loaded with two pots
            
  Input: Simulated sensor input, two pot locations of tray directly below pot dispenser
            
  Output: Pot dispenser will dispense two pots into designated pot locations on tray
  
  Test Case Derivation: Pot dispenser will dispense pots into correctly positioned tray as it is prompted to
            
  How test will be performed: Tray will be manually placed directly below pot dispenser with pot locations 
  directly below pot stack. Machine will be turned on. Once pots are dispensed, pot dispenser will 
  queue next two pots and tray will be removed.\\

  \item{PDST-02: \textbf{Tray Sensing}}
  
  Control: Dynamic, Manual
            
  Initial State: Mounted sensor with no object being sensed
            
  Input: Manual placement of trays in front of sensor
            
  Output: Sensor will output a signal when the presence of a tray is sensed
  
  Test Case Derivation: Sensor will recognize that a tray is beneath the pot dispenser
            
  How test will be performed: Tray will be manually placed directly in front of the mounted sensor. Signal 
  output from sensor will be analyzed to determine sensor is aware of tray presence. Tray will then be 
  moved forward and output from sensor will be analyzed to confirm sensor is aware that tray is moving. 
  Tray will then be moved forward out of view of sensor and output from sensor will be analyzed to confirm 
  snesor is aware that tray is no longer present.\\

  \item{PDST-03: \textbf{Ability to Dispense 4" Diameter Pots}}
  
  Control: Static, Manual

  How test will be performed: All specifications of pot dispenser will ensure that a 4" diameter pot is able 
  to be dispensed. Measurements and reviews will be conducted by another member of the group any time a change 
  is made to the dispenser during design and build phases. During build phase, test will be conducted on both 
  pot dispensers.\\

  \item{PDST-04: \textbf{Ability to Store/Sispense Multiple Pots}}
  
  Control: Dynamic, Manual

  Initial State: Pot dispenser loaded with pots

  Input: Ten pots, simulated sensor input

  Output: Pot dispenser will dispense two pots, reload with two pots from stack, dispense two pots, etc. until
  pot storage is empty

  Test Case Derivation: Pot dispenser will complete 5 cycles of dispensing, storing and dispensing 10 pots in total

  How test will be performed: Pot dispenser will be loaded with 10 pots, 5 per side. Sensor input will be simulated
  to indicate presence of tray. Pot dispenser will complete 5 cycles of dispensing, at which point pot storage will
  be spent.\\
  
  \item{PDST-05: \textbf{Pot Storage Detection}}
  
  Control: Dynamic, Manual

  Initial State: Pot dispenser with no pots in storage

  Input: N/A

  Output: Pot storage sensor will output a signal when no trays are detected in pot storage

  Test Case Derivation: Sensor will recognize that no pots are sensed in pot storage

  How test will be performed: All pots will be removed from pot storage. Signal output from sensor will be
  analyzed to confirm sensor is aware that pot storage is empty.\\

\end{enumerate}

\subsubsection{Conveyor Subsystem Testing}

\begin{enumerate}
\item{CST-01: \textbf{Conveyor Ability to Move Trays}}

Control: Dynamic, Manual

Initial State: Conveyor with tray placed at start

Input: Simulated inputs indicating conveyor can start

Output: Constant speed of conveyor motor and belt

Test Case Derivation: Conveyor will recognize tray is present on belt and able to move forward

How test will be performed: A single tray will be placed at the start point on the conveyor belt. The conveyor 
will receive signals indicating that there are no issues with any other subsystems and the tray can be moved 
forward. Behaviour of conveyor will be observed to confirm conveyor has moved tray from start to end with no 
stopping. Test will be interrupted if tray is unable to move forward due to physical interferance or if conveyor stops.
\\
\item{CST-02: \textbf{Conveyor Ability to Stop}}

Control: Dynamic, Manual

Initial State: Conveyor moving tray along belt

Input: Simulated signals from pot dispenser indicating tray is beneath pot dispenser

Output: Conveyor motor and belt come to a stop

Test Case Derivation: Conveyor will receive signal from pot dispenser, indicating the tray is beneath the pot
dispenser, and stop movement of tray

How test will be performed: A single tray will be placed on the conveyor while conveyor is moving. A signal will be 
sent to the conveyor, simulating a signal from the pot dispenser sensor which indicates that the tray is beneath 
the pot dispenser. Behaviour of conveyor will be observed o confirm conveyor brings tray to a stop when signal is 
recognized.\\

\item{CST-03: \textbf{Conveyor Belt Friction}}

Control: Static, Manual

Input: Mass of tray, tilt angle of conveyor belt

Output: Maximum acceleration of conveyor belt

Test Case Derivation: Maximum acceleration based on friction between conveyor belt and tray will be calculated 
and set acceleration/decceleration values will be determined

How test will be performed: 6 trays will be weighed and the mean mass will be calculated. Each tray will be placed on 
the conveyor belt one by one. For each tray, the conveyor belt will be tilted until the tray begins to slip, at which
point the angle at which the belt is tilted will be recorded. The mean of these 6 angles will be calculated. These values
will then be used to approximately determine the maximum acceleration the trays can undergo without slipping, and the
acceleration of the conveyor motor will be set to not exceed 70\% of this value.
\\
\end{enumerate}

\subsubsection{Verification Subsystem Testing}

\begin{enumerate}
  \item{VST-01: \textbf{Verify Correct Number of Pots in Tray}}
  
  Control: Dynamic, Manual
            
  Initial State: One tray filled with some pots placed on the conveyor.
            
  Input: Tray filled with a number of pots.
            
  Output: Sends a signal to microcontroller if the tray is not filled with pots, 
  does not send a signal if all pot locations on the tray are filled.
  
  Test Case Derivation: The sensor signal will ensure all trays leaving the conveyor 
  have been successfully filled with pots.
            
  How test will be performed: All other sensors and subsystems will be switched off. 
  The subsystem will be manually activated to identify pots in the given tray as it moves on the conveyor.
  The success or failure will be observed.\\

\end{enumerate}

\subsection{Tests for Nonfunctional Requirements}

\subsubsection{Safety Critical Testing}

\begin{enumerate}

  \item{SCT-01: \textbf{Tray Dispenser Failure}}

  Type: Dynamic, Manual
					
  Initial State: Tray dispenser functioning normally
					
  Input: Tray dispenser disconnect
					
  Output: System flags tray dispenser failure
					
  How test will be performed: Tray dispenser will be manually disconnected from the system during operation. System response 
  will be analyzed to confirm that a failure in the tray dispenser is recognized.
\\		
  \item{SCT-02: \textbf{Pot Dispenser Failure}}

  Type: Dynamic, Manual
					
  Initial State: Pot dispenser functioning normally
					
  Input: Pot dispenser disconnect
					
  Output: System flags pot dispenser failure
					
  How test will be performed: Pot dispenser will be manually disconnected from the system during operation. System response 
  will be analyzed to confirm that a failure in the pot dispenser is recognized.
\\
  \item{SCT-03: \textbf{Conveyor Failure}}

  Type: Dynamic, Manual
					
  Initial State: Conveyor functioning normally
					
  Input: Conveyor disconnect
					
  Output: System flags conveyor failure
					
  How test will be performed: Conveyor will be manually disconnected from the system during operation. System response 
  will be analyzed to confirm that a failure in the conveyor is recognized.
\\
  \item{SCT-04: \textbf{Verification Failure}}

  Type: Dynamic, Manual
					
  Initial State: Verification functioning normally
					
  Input: Verification disconnect
					
  Output: System flags verification failure
					
  How test will be performed: Verification will be manually disconnected from the system during operation. System response 
  will be analyzed to confirm that a failure in the verification is recognized.

\end{enumerate}

\subsubsection{Precision Testing}

\begin{enumerate}

  \item{PT-01: \textbf{Tray Dispenser Precision}}
  
  Type: Static, Manual

  How test will be performed: Tray storage will be filled to maximum capacity. Tray dispenser will place tray onto conveyor belt. 
  Centre line of tray will be established and measured relative to centre line of conveyor. Test will be repeated for all trays 
  until tray storage is empty. Average offset measurement will be calculated.
\\
  \item{PT-02: \textbf{Pot Dispenser Precision}}

  Type: Static, Manual

  How test will be performed: Pot storage will be filled to 50\% capacity. Pot dispenser will dispense pots into trays. Centred 
  position of each opening in trays will be established and measured relative to centre line of pots. Test will be repeated for all
  pots until pot storage is empty. Average offset measurement will be calculated.
  
\end{enumerate}

\subsubsection{Reliability Testing}

\begin{enumerate}

  \item{RT-01: \textbf{Function Under Vibration}}
  
  Type: Static, Manual

  How test will be performed: Pot-pulator will run continuously for 8 hours, with a tester ensuring pots and trays are available to the 
  machine at all times so operation is never interrupted. Machine will be subject to vibrations resulting from conveyor motor, tray dispenser
  motors, and pot dispenser motors. Behaviour will be observed to ensure machine is able to function under long-term exposure to small amplitude 
  vibration.
\end{enumerate}

\subsubsection{Expected Physical Environment Testing}

\begin{enumerate}

  \item{EPET-01: \textbf{Function Under Aerial Pollution}}
  
  Type: Static, Manual

  How test will be performed: Pot-pulator will run continuously for 8 hours in an environment with an amount of aerial pollution similar to 
  what is expected of the environment at Sheridan Nursery. A tester will be present to ensure that pots and trays are available to the machine
  at all times so operation is never interrupted. Behaviour will be observed to ensure machine is able to function for a long period of time in 
  an environment with aerial pollution.

\end{enumerate}

\subsubsection{Speed Requirements Testing}
\begin{enumerate}
  \item{SRT-01: \textbf{Acceleration Displacement of Trays}}
  
Type: Dynamic, Manual

Initial State: Multiple trays (2-3) on the conveyor.

How test will be performed: The conveyor speed and acceleration will be modified while 
trays are on it. The trays should not show perpendicular axis movement along the conveyor
while in higher than normal speeds.
\\
\item{SRT-02: \textbf{Pot Dispensing Rate}}
  
Type: Dynamic, Automatic

Initial State: Subsystem in idle state ready to dispense pots.

Input: Stack of pots.

Output: Pots dispensing.

Test Case Derivation: The preceding system for filling pots with soil operates at a certain rate which
should be met by the Pot-purlator.

How test will be performed: Pots will be placed in the stack. When turned on, the pots will dispense
at the desired rate (10 pots / 30 sec) and timed using a stopwatch. If the dispenser can meet
these requirements then it passes.
\\
\item{SRT-02: \textbf{Tray Dispensing Rate}}
  
Type: Dynamic, Automatic

Initial State: Subsystem in idle state ready to dispense trays.

Input: Stack of Trays.

Output: Trays dispensing.

Test Case Derivation: The preceding system for filling pots with soil operates at a certain rate which
should be met by the Pot-purlator.

How test will be performed: Trays will be placed in the stack. When turned on, the trays will dispense
at the desired rate (1 tray / 30 sec) and timed using a stopwatch. If the dispenser can meet
these requirements then it passes.

\end{enumerate}

\subsubsection{Learning Requirements Testing}
\begin{enumerate}
  \item{LRT-01: \textbf{Operational Simplicity}}
  
Type: Static				
					
How test will be performed: An individual will be trained on operating the entire system.
After training is complete, the individual must demonstrate that they are able to 
successfully and safely handle all possible scenarios that may occur during operation.
\end{enumerate}

\subsubsection{Accessibility Requirements Testing}
\begin{enumerate}
  \item{ART-01: \textbf{Audio and Visual Indicators}}
  
Type: Static, Manual

Inputs: Trigger signal.

Outputs: A corresponding light, sound, or screen display.

How test will be performed: LEDs, speakers, and LCD screens will be placed in the
system and sent a signal to activate in a specified way.
\end{enumerate}

\subsection{Traceability Between Test Cases and Requirements}
The following table outlines all of the system tests and how they relate to the
relevent requirements. The requirements can be referenced in the SRS document.\\

\begin{longtable}{ |p{4cm}|p{8cm}|  }
  \caption{Corresponding Test IDs and Requirements}
  \label{tab:Table1}\\
  
  \hline
  \textbf{Test ID} & \textbf{Supporting Requirements}\\
  \hline
  TDST-01 &  TDR3, TDR5\\
  \hline
  TDST-02 &  TDR4, TDR5 \\
  \hline
  TDST-03 &  TDR2 \\
  \hline
  TDST-04 &  TDR2 \\
  \hline
  PDST-01 &  PDR2 \\
  \hline
  PDST-02 &  PDR2 \\
  \hline
  PDST-03 &  PDR3 \\
  \hline
  PDST-04 &  PDR4 \\
  \hline
  PDST-05 &  PDR5, PDR6 \\
  \hline
  PCST-01 &  TDR1 \\
  \hline
  PCST-02 &  TDR5, TDR6 \\
  \hline
  PCST-03 &  TDR7 \\
  \hline
  PCST-04 &  PDR1 \\
  \hline
  PCST-05 &  PDR6, PDR7 \\
  \hline
  PCST-06 &  PDR8 \\
  \hline
  PCST-07 &  CR1 \\
  \hline
  PCST-08 &  CR5 \\
  \hline
  PCST-09 &  CR6 \\
  \hline
  VST-01 &  VR1 \\
  \hline
  VST-02&  VR2 \\
  \hline
  SCT-01 &  NFR12 \\
  \hline
  SCT-02 &  NFR12 \\
  \hline
  SCT-03 &  NFR12 \\
  \hline
  SCT-04 &  NFR12 \\
  \hline
  PT-01 & NFR13 \\
  \hline
  PT-02 & NFR14 \\
  \hline
  RT-01 & NFR17 \\
  \hline
  EPET-01 & NFR20 \\
  \hline
  LRT-01&  NFR6 \\
  \hline
  ART-01 & NFR7 \\
  \hline
  SRT-01 & NFR8 \\
  \hline
  SRT-02 & NFR9 \\
  \hline
  SRT-03 & NFR10 \\
  \hline
\end{longtable}

\newpage

\section{Unit Test Description}

The following section includes testing that was performed on critical hardware
components of the system. These tests were performed for the purpose
of verifying and understanding the behaviour of each hardware component.

\subsection{Unit Testing Scope}

Modules will be tested based on the functionality of hardware with which they are interacting. 
For this reason, the Communication Module will be tested through each test. The Front End and Verification Analysis Modules have 
undergone constant testing and verification through the design of the user interface, and will therefore not require 
additional testing initiatives. Additionally, unit tests will be responsible for testing multiple modules at once due 
to the repeated use of hardware components.

\subsection{Tests for Functional Requirements}

\indent \subsubsection{Pot Dropping Input, Pot Dropping Position, Tray Dispenser Input, Verification Output Modules}

\begin{enumerate}

  \item{HWT-01: \textbf{Ultrasonic Range Finder Control}}
  
Type: Dynamic\\
Initial State: Sensor mounted with no object placed in front of sensor, serial monitor outputting
 current distance reading.\\
Input: Object placed directly in front of sensor.\\
Output: Serial monitor displays current distance reading.\\
Test Case Derivation: Change in distance read will ensure sensor is accurately reading the distance 
between itself and the object, distance will be verified through measurement.
How test will be performed: Object will be placed in front of sensor, a measuring tool will be used to 
measure distance between the object and the sensor, will verify if serial monitor output is accurate and precise.\\

\subsubsection{Pot Dropping Stepper, Pot Dropping Output, Tray Dispenser Output Modules}
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

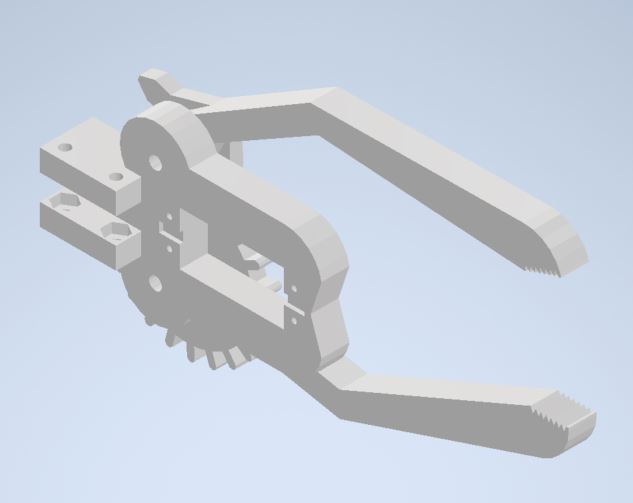
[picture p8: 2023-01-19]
docs/Design/SystDesign/images/Tray_Dropper.JPG

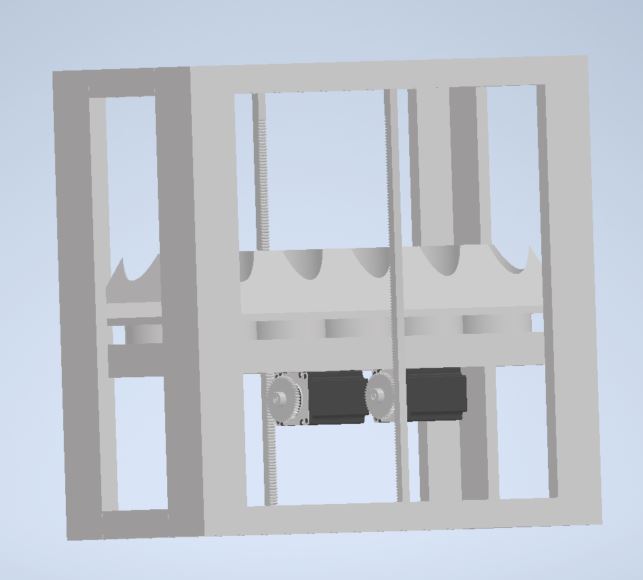
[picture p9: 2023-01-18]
docs/Design/SystDesign/images/Tray_Elevator.JPG

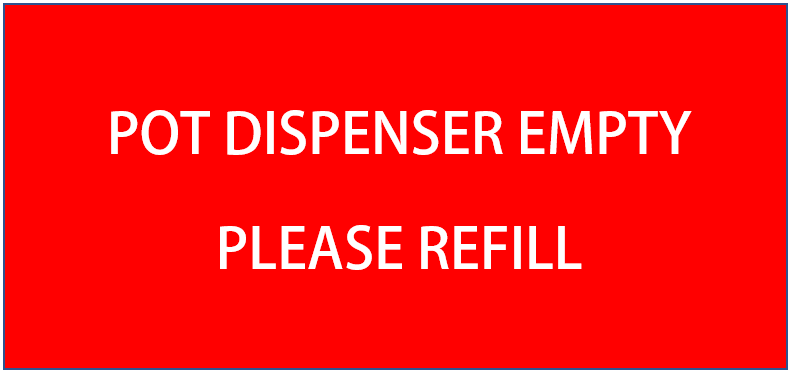
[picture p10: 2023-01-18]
docs/Design/SystDesign/images/interface1.png

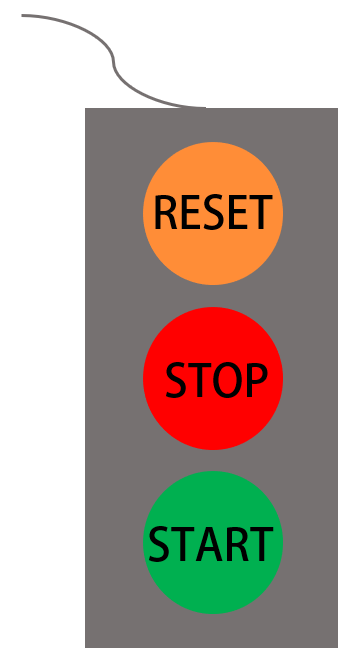
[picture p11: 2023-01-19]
docs/Design/SystDesign/images/interface2.PNG

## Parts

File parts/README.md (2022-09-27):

This folder will contain all CAD parts/assemblies as well as ordered parts.

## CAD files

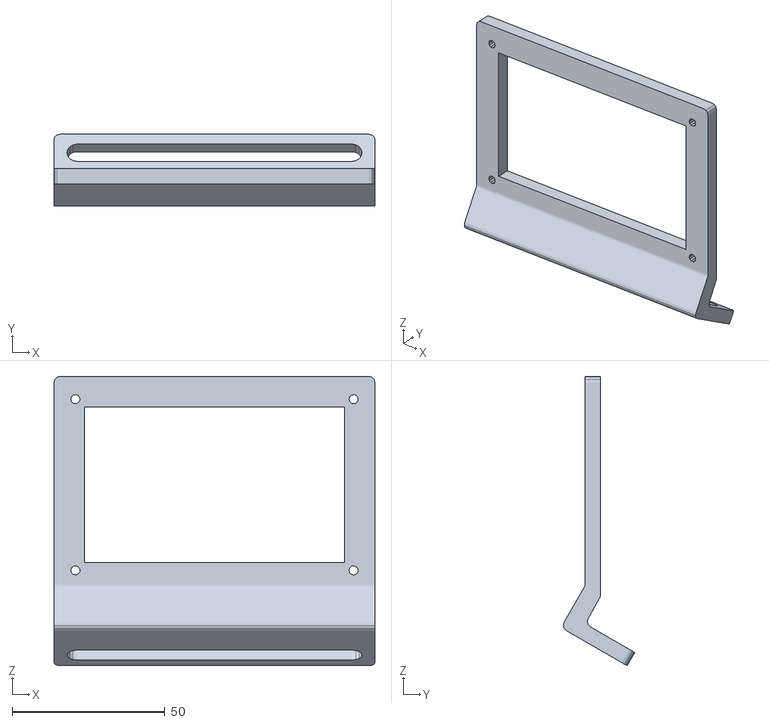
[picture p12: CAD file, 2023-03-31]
parts/General Assembly/screen mount.stl
105.0 x 23.4 x 94.7

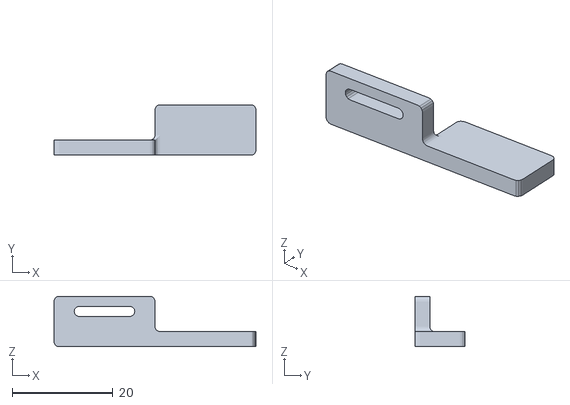
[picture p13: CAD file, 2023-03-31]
parts/Pot Dropper/servo attachment.stl
40.0 x 10.0 x 10.0

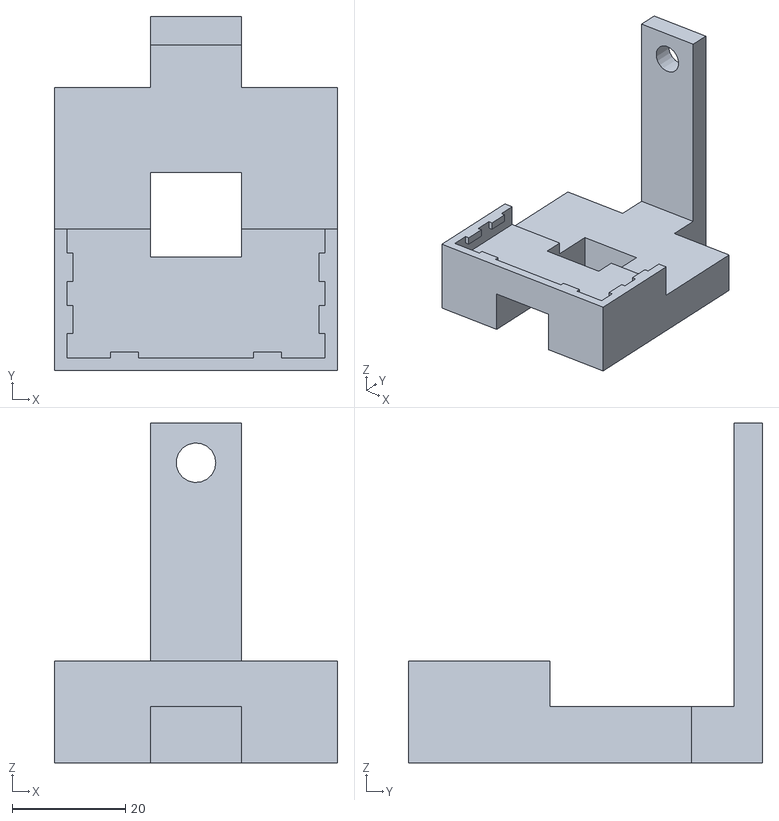
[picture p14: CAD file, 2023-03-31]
parts/Tray Dropper/ALTERNATIVE SOLUTION/sensor mount.stl
50.0 x 62.5 x 60.0

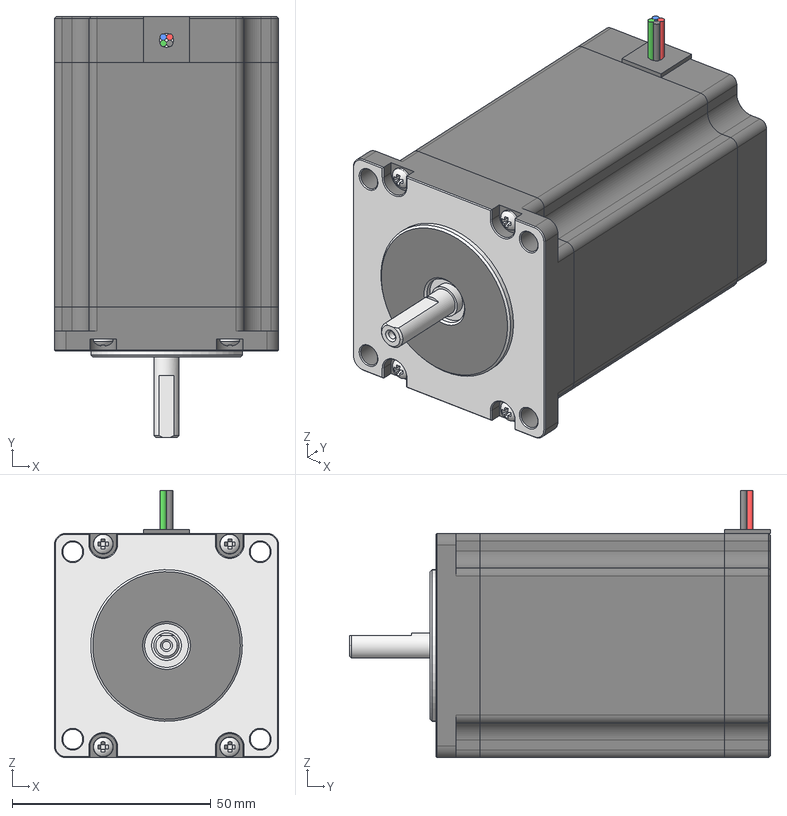
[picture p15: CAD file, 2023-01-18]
parts/Tray Elevator/NEMA 23 84mm Frame Stepper Motor.step
56.4 x 105.8 x 67.2 mm
Main Body
Cap
Screw 2
Screw 3
Screw 4
Strain Relief
Armature
Wire - Black
Screw 1
Wire - Green
Wire - Blue
Wire - Red

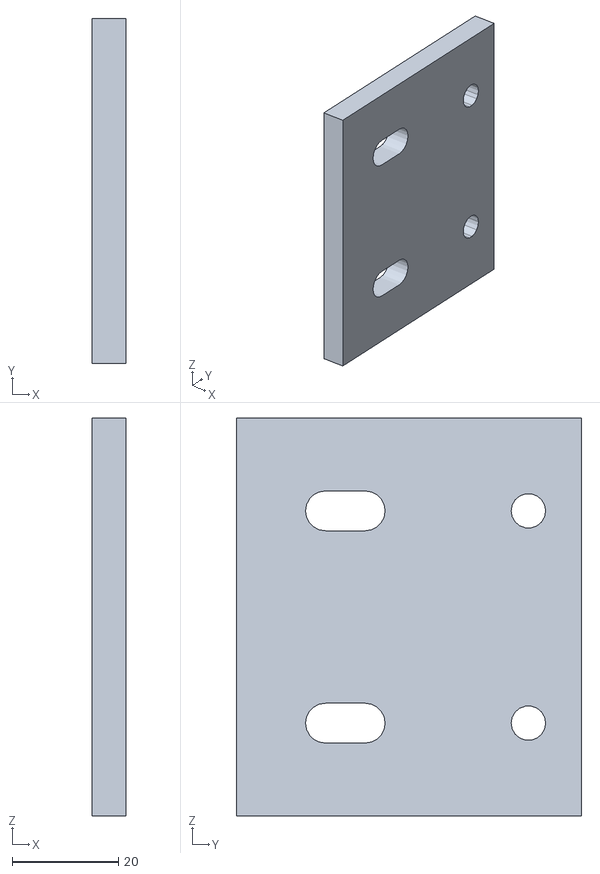
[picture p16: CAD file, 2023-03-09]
parts/General Assembly/mounting bracket 1.stl
6.35 x 65.0 x 75.0

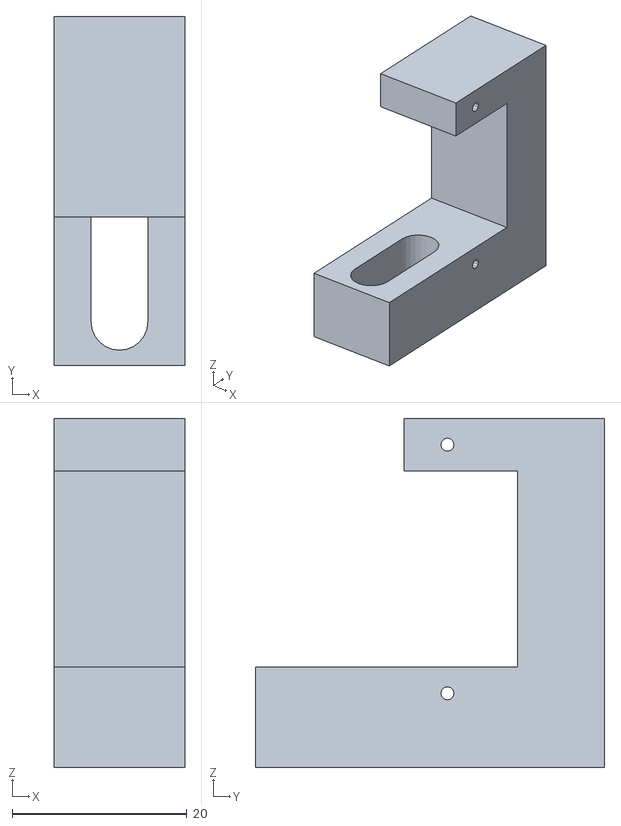
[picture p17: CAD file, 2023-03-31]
parts/Pot Dropper/servo mount.stl
15.0 x 40.0 x 40.0

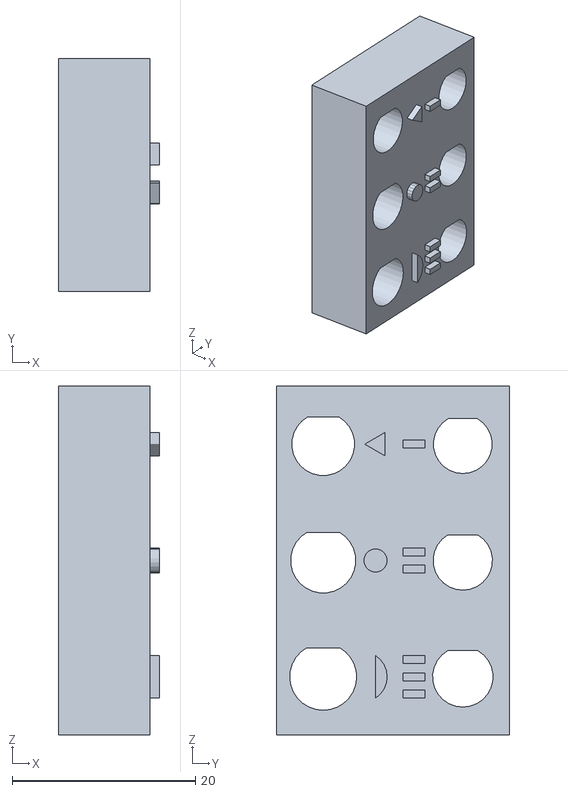
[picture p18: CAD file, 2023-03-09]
parts/Tray Dropper/ALTERNATIVE SOLUTION/shaft hole tester.stl
11.0 x 25.4 x 38.1

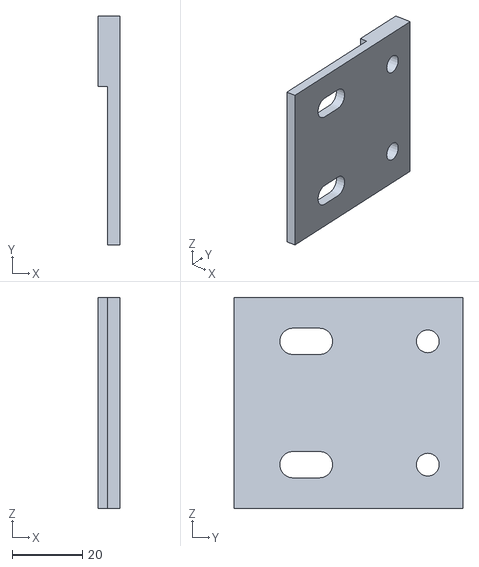
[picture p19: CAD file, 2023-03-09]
parts/General Assembly/mounting bracket 2.stl
6.35 x 65.0 x 60.0

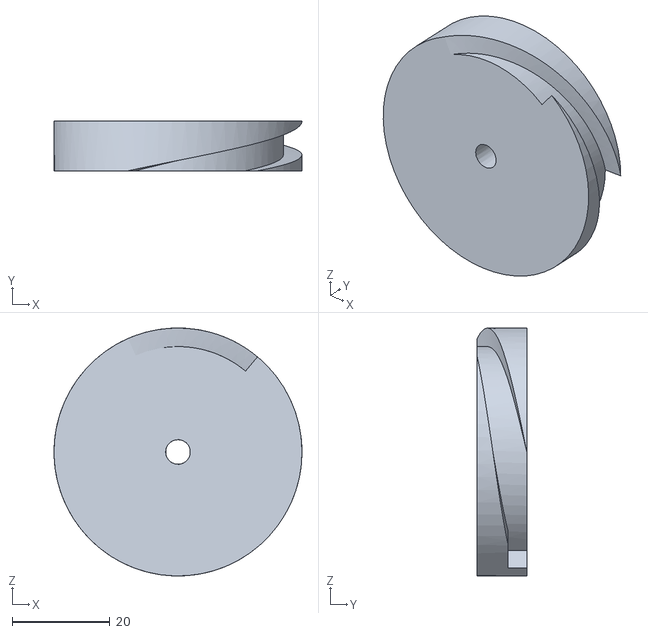
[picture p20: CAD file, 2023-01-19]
parts/Pot dropper/pot dropper.stl
50.8 x 10.2 x 50.8

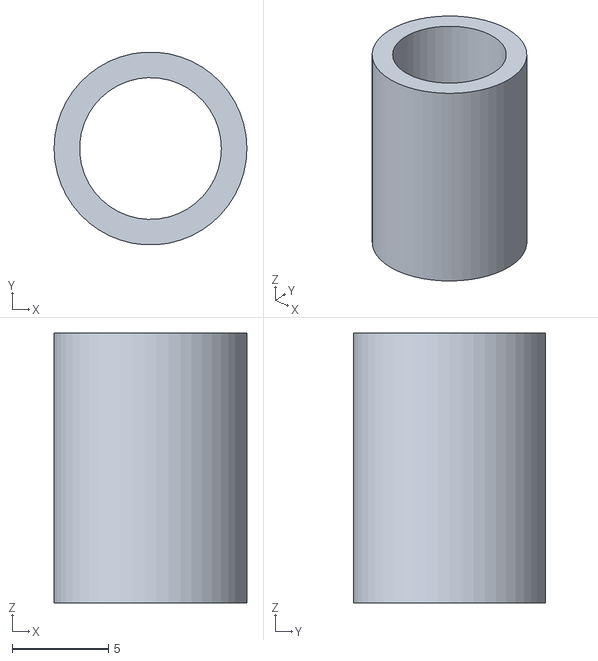
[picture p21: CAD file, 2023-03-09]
parts/Tray Dropper/ALTERNATIVE SOLUTION/spacer.stl
10.0 x 9.98 x 14.0

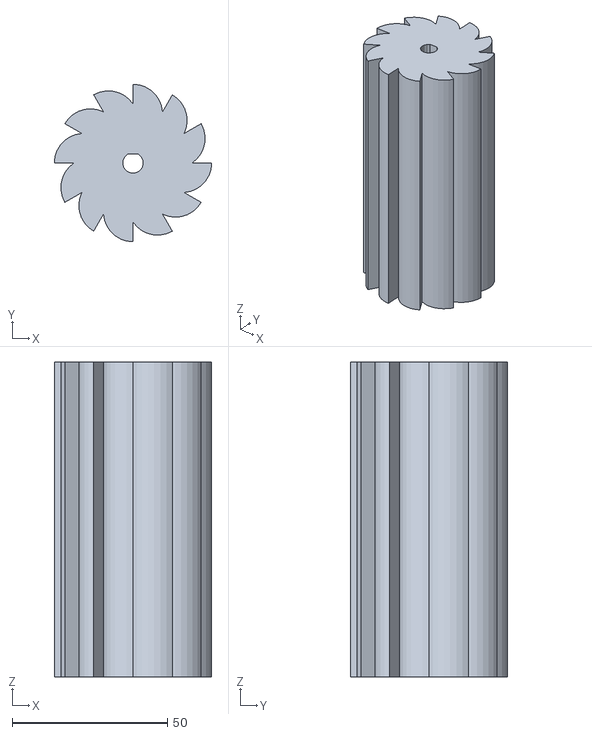
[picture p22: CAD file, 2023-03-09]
parts/Tray Dropper/ALTERNATIVE SOLUTION/THE_WHEEL 2.0.stl
50.8 x 50.8 x 101.6

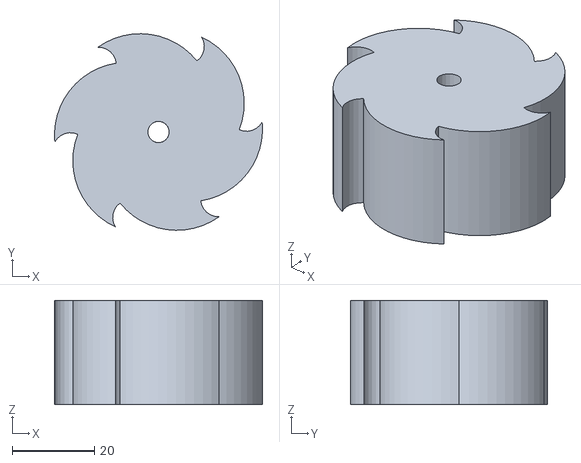
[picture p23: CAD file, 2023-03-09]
parts/Tray Dropper/ALTERNATIVE SOLUTION/THE_WHEEL.stl
50.7 x 47.9 x 25.4

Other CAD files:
parts/General Assembly/OldVersions/screen mount.0003.ipt
parts/General Assembly/mounting bracket 1.ipt
parts/General Assembly/mounting bracket 2.ipt
parts/General Assembly/screen mount.ipt
parts/Pot Dropper/servo attachment.ipt
parts/Pot Dropper/servo mount.ipt
parts/Pot dropper/pot dropper.ipt
parts/Tray Dropper/ALTERNATIVE SOLUTION/OldVersions/THE_WHEEL 2.0.0005.ipt
parts/Tray Dropper/ALTERNATIVE SOLUTION/OldVersions/Tray_Dropper_Asm.0001.iam
parts/Tray Dropper/ALTERNATIVE SOLUTION/OldVersions/WHEEL X SHAFT.0003.iam
parts/Tray Dropper/ALTERNATIVE SOLUTION/OldVersions/sensor mount.0001.ipt
parts/Tray Dropper/ALTERNATIVE SOLUTION/OldVersions/shaft hole tester.0001.ipt
parts/Tray Dropper/ALTERNATIVE SOLUTION/OldVersions/spacer.0001.ipt
parts/Tray Dropper/ALTERNATIVE SOLUTION/THE_WHEEL 2.0.ipt
parts/Tray Dropper/ALTERNATIVE SOLUTION/THE_WHEEL.ipt
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

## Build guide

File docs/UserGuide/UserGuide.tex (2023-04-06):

\documentclass[12pt, titlepage]{article}

\usepackage{booktabs}
\usepackage{graphicx}
\usepackage{tabularx}
\usepackage{hyperref}
\usepackage[english]{babel}
\usepackage{enumitem}
\usepackage{pdflscape}
\usepackage{array}
\usepackage{longtable}
\graphicspath{ {./images/} }
\usepackage{float}
\usepackage{fullpage}
\usepackage[round]{natbib}
\usepackage{multirow}
\usepackage{booktabs}
\usepackage{tabularx}
\usepackage{graphicx}
\graphicspath{ {./images/} }
\usepackage{float}
\usepackage{hyperref}
\hypersetup{
    colorlinks=true,       % false: boxed links; true: colored links
    linkcolor=red,          % color of internal links (change box color with linkbordercolor)
    citecolor=green,        % color of links to bibliography
    filecolor=magenta,      % color of file links
    urlcolor=cyan           % color of external links
}

\newcounter{srreqnum} %Likely change number
\newcommand{\lthesrreqnum}{LC\thesrreqnum}
\newcommand{\srref}[1]{SR\ref{#1}}

\title{The Pot-pulator User Guide}

\author{Aaron Billones, billonea\\Gillian Ford, fordg\\Juan Moncada, moncadaj\\Steven Ramundi, ramundis}

\date{April 5, 2023}

\input{../Comments}
\input{../Common}

\begin{document}

\maketitle
\thispagestyle{empty}

\pagenumbering{roman}

\begin{tabularx}{\textwidth}{p{3cm}p{4cm}X}
    \toprule {\bf Date} & {\bf Version} & {\bf Notes}\\
    \midrule
    2023-04-05 & Aaron Billones,& Initial release\\&Gillian Ford,\\&Juan Moncada,\\&Steven Ramundi \\
    
    \bottomrule
\end{tabularx}

~\newpage

\tableofcontents

~\newpage

\pagenumbering{arabic}

\section{Introduction}

Welcome to the user manual for the Pot-pulator - a machine designed to assist Sheridan Nurseries in populating their trays with pots, in preparation for planting with soil and seeds. The Pot-pulator is used to automate this process to reduce the need for manual labour, improving efficiency and productivity in the nursery. This manual will provide guidance on the continuous operation of the Pot-pulator, providing the information needed to effectively utilize this powerful tool.

\section{Getting started}

\subsection{Operation Steps}
When using the Pot-pulator, start by fulling the machine with trays in the tray dropper section, and empty pots in the pot dropper section. The tray dropper can hold 30 trays, while the pot dropper can hold up to 300 pots, requiring refills every 15 minutes. Within this time, the machine requires no further action from the user once the on button has been pressed. Under normal operation, the Pot-pulator will follow the steps below:
\\ 
\begin{enumerate}
\item Fill the machine with empty pots and trays 
\item Set both switches on the conveyer down, starting with the black one, then the red.

\item Tray dropper will dispense trays one at a time

\item A tray will drop onto the conveyer belt and move to the next section

\item Conveyer positions the tray to prepare for pot dropping

\item Conveyer stops and drops 2 pots at a time into the tray

\item Conveyer continues to move to the next available slots in the tray, until the entire tray is filled with pots (10 pots)

\item The verification subsystem will determine if all the pots have been placed correctly in the tray, outputting an LED when a pot is missing or out of place. \\
\end{enumerate}

\noindent Throughout the operation of the device, the user interface will display the current status of the machine. To learn more about the user interface and how to navigate it, please refer to the "User Interface" section of this manual.
\subsection{Safety and Precautions}
When refilling pots and trays, ensure that the machine is turned off. Once they have been loaded into the system, the user can then turn on the machine for operation.
\section{User Interface}
\begin{figure}[H]
    \centering
    
    \caption{User Interface when system is functioning normally}
    \label{fig:scope}
  \end{figure}

  \begin{figure}[H]
    \centering
    
    \caption{User Interface when errors arise}
    \label{fig:scope}
  \end{figure}
The user interface includes a screen with the output functions of the machine. The user does not have to interact with this device, as it is only used to provide information on the status of the Pot-pulator.
\subsection{Master Switch Status}
This section informs the user if the machine is on or off.
\subsection{Restock Status}
This section informs the user that the tray or pot dispenser is empty. The user will need to refill the pot dropper and the tray dispenser every 15 minutes.
\subsection{Verification}
This section informs the user if there is a pot missing or out of place once the trays reach the verification system.
\subsection{Jam Status}
This section informs the user that there is a jam in the stack of trays in the tray dispenser, or the stack of pots in the pot dropper. This will require the machine to be turned off and the trays and pots to be taken out and restacked. 
\newpage
\section{Features and Functionality}
\subsection{Conveyer}
To start the Pot-pulator, the user needs to press two switches located on the conveyer belt. Properly using these switches is crucial for the smooth operation of the machine. First, the black power switch should be pressed down to the line, then the red switch should be pressed down to the two lines. This ensures that the machine is ready to start and will function as needed.
\\
\noindent Once the switches have been set correctly, the conveyer belt will begin to move the trays through each system in the Pot-pulator. The conveyer will start and stop at specific positions to ensure that each tray is correctly positioned for pot dropping. This ensures that the system operates smoothly and that the pots are accurately placed in each tray.
\\
\noindent It's important to note that the conveyer belt must be properly maintained to ensure its longevity and proper functioning. Users should regularly clean it to remove any dirt, debris, or other materials that may accumulate on the belt. Additionally, users should inspect the conveyer belt regularly to ensure that it is functioning correctly.

\begin{figure}[H]
    \centering
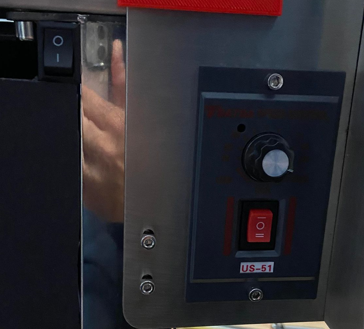
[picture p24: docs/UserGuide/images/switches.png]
    
    \caption{Both black and red switches should be switched down for proper function. This figure shows the Pot-Pulator powered off.}
    \label{fig:scope}
  \end{figure}
\newpage
\subsection{Tray Dispenser}
When using the tray dispenser system, it's important to note that up to 30 trays can be manually inserted into the top of the machine at the beginning of each refill. This allows for a continuous flow of trays, ensuring that there will be enough available for continuous use.
\\
\noindent The tray dispenser will need to be refilled every 15 minutes. This ensures that the machine doesn't run out of trays, which can cause delays and decrease the overall time efficiency of the device.
\\
\noindent To ensure proper functionality, it's recommended that the trays be stacked and placed evenly into the machine. This not only helps with the flow of trays through the dispenser, but also prevents jams and other issues that can arise from uneven stacking.
\\
\noindent By following these guidelines, users can ensure smooth and efficient tray dispensing, minimizing any downtime caused by errors.

\begin{figure}[H]
    \centering
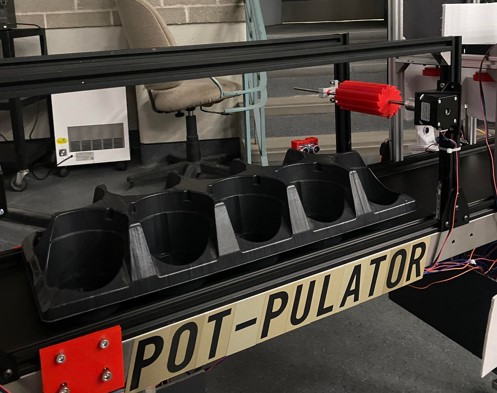
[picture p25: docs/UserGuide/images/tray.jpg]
    
    \caption{Tray Dispenser}
    \label{fig:scope}
  \end{figure}
\newpage
\subsection{Pot Dropper}
When using pot dropper system, the user can insert up to 300 pots manually into the uppermost section of the machine. Every 15 minutes, it is required for the user to refill the pot dropper to guarantee smooth operation of the device.
\\
\noindent It is important to note that the pot dropper contains two sections, each of which can accommodate a certain number of pots. To optimize the efficiency of the machine and guarantee an even distribution of pots, it is recommended that users stack and place pots in both sections uniformly. Proper stacking and placement of pots into the machine helps to prevent any issues such as jamming, or other operational malfunctions.
\\
\noindent By adhering to these guidelines, users can expect a reliable, efficient, and uninterrupted experience while using the pot dropper.

\begin{figure}[H]
    \centering
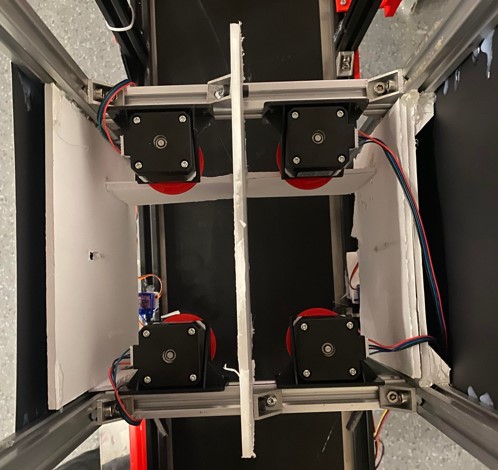
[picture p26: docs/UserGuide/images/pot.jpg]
    
    \caption{Pot Dropper}
    \label{fig:scope}
  \end{figure}
\newpage
\subsection{Verification System}
The verification system will notify the user when there is a problem with the system. If there is a pot missing or out of place, an LED will light up, alerting the user that the system is not functioning as intended. 
\section{Troubleshooting and FAQs}
\subsection{What happens if trays get stuck?}
If the trays get stuck, turn off the machine and remove them from the stack, and refill them evenly. Once they are in place, turn the machine on to run as normal.
\subsection{What happens if pots get stuck?}
If the pots get stuck, turn off the machine and remove them from the stack, and refill them evenly into both sections of the pot dropper. Once they are in place, turn the machine on to run as normal.
\subsection{How many trays can the tray dropper hold?}
The tray dropper can hold up to 30 trays, but it will need to be refilled every 15 minutes.
\subsection{How many pots can the pot dropper hold?}
The pot dropper can hold up to 300 pots, but it will need to be refilled every 15 minutes.
\subsection{How will I know that all the pots have been placed correctly in the tray?}
The verification subsystem will determine if all the pots have been placed correctly in the tray, outputting an LED and an error on the user interface when a pot is missing or out of place.
\subsection{How do I refill the Pot-pulator with trays and pots?}
When refilling pots and trays, ensure that the machine is turned off. 30 Trays and 300 pots can then be loaded evenly into their respective sections, the user can then turn on the machine for operation. The pot dropper has two sections, and the user can distribute them evenly between them.
\subsection{How do I use the user interface of the Pot-pulator?}
The user interface will display the current status of the machine. To learn more about the user interface and how to navigate it, please refer to the "User Interface" section of the manual.

\end{document}

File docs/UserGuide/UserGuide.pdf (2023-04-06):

# The Pot-pulator User Guide

### Aaron Billones, billonea Gillian Ford, fordg Juan Moncada, moncadaj Steven Ramundi, ramundis

### April 5, 2023

Date | Version | Notes
2023-04-05 | Aaron Billones, | Initial release
| Gillian Ford, Juan Moncada, Steven Ramundi

## Contents

1 Introduction | 1
2 Getting started | 1
3 User Interface | 2
4 Features and Functionality | 4
5 Troubleshooting and FAQs | 7
5.5 How will I know that all the pots have been placed correctly in the tray? . . | 7

ii

## 1 Introduction

Welcome to the user manual for the Pot-pulator - a machine designed to assist Sheridan Nurseries in populating their trays with pots, in preparation for planting with soil and seeds. The Pot-pulator is used to automate this process to reduce the need for manual labour, improving efficiency and productivity in the nursery. This manual will provide guidance on the continuous operation of the Pot-pulator, providing the information needed to effectively utilize this powerful tool.

## 2 Getting started

### 2.1 Operation Steps

When using the Pot-pulator, start by fulling the machine with trays in the tray dropper section, and empty pots in the pot dropper section. The tray dropper can hold 30 trays, while the pot dropper can hold up to 300 pots, requiring refills every 15 minutes. Within this time, the machine requires no further action from the user once the on button has been pressed. Under normal operation, the Pot-pulator will follow the steps below:

1. Fill the machine with empty pots and trays
2. Set both switches on the conveyer down, starting with the black one, then the red.
3. Tray dropper will dispense trays one at a time
4. A tray will drop onto the conveyer belt and move to the next section
5. Conveyer positions the tray to prepare for pot dropping
6. Conveyer stops and drops 2 pots at a time into the tray
7. Conveyer continues to move to the next available slots in the tray, until the entire tray is filled with pots (10 pots)
8. The verification subsystem will determine if all the pots have been placed correctly in the tray, outputting an LED when a pot is missing or out of place.

Throughout the operation of the device, the user interface will display the current status of the machine. To learn more about the user interface and how to navigate it, please refer to the ”User Interface” section of this manual.

### 2.2 Safety and Precautions

When refilling pots and trays, ensure that the machine is turned off. Once they have been loaded into the system, the user can then turn on the machine for operation.

1

## 3 User Interface

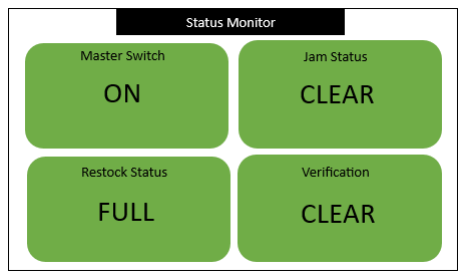
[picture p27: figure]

Figure 1: User Interface when system is functioning normally

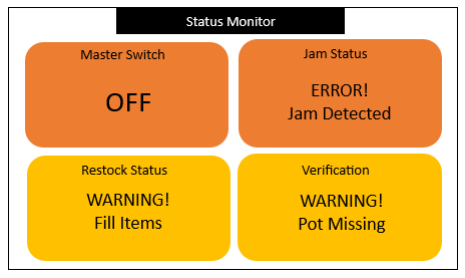
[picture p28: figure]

Figure 2: User Interface when errors arise

The user interface includes a screen with the output functions of the machine. The user does not have to interact with this device, as it is only used to provide information on the status of the Pot-pulator.

2

### 3.1 Master Switch Status

This section informs the user if the machine is on or off.

### 3.2 Restock Status

This section informs the user that the tray or pot dispenser is empty. The user will need to refill the pot dropper and the tray dispenser every 15 minutes.

### 3.3 Verification

This section informs the user if there is a pot missing or out of place once the trays reach the verification system.

### 3.4 Jam Status

This section informs the user that there is a jam in the stack of trays in the tray dispenser, or the stack of pots in the pot dropper. This will require the machine to be turned off and the trays and pots to be taken out and restacked.

3

## 4 Features and Functionality

### 4.1 Conveyer

To start the Pot-pulator, the user needs to press two switches located on the conveyer belt. Properly using these switches is crucial for the smooth operation of the machine. First, the black power switch should be pressed down to the line, then the red switch should be pressed down to the two lines. This ensures that the machine is ready to start and will function as needed.
Once the switches have been set correctly, the conveyer belt will begin to move the trays through each system in the Pot-pulator. The conveyer will start and stop at specific positions to ensure that each tray is correctly positioned for pot dropping. This ensures that the system operates smoothly and that the pots are accurately placed in each tray.
It’s important to note that the conveyer belt must be properly maintained to ensure its longevity and proper functioning. Users should regularly clean it to remove any dirt, debris, or other materials that may accumulate on the belt. Additionally, users should inspect the conveyer belt regularly to ensure that it is functioning correctly.


Figure 3: Both black and red switches should be switched down for proper function. This figure shows the Pot-Pulator powered off.

4

### 4.2 Tray Dispenser

When using the tray dispenser system, it’s important to note that up to 30 trays can be manually inserted into the top of the machine at the beginning of each refill. This allows for a continuous flow of trays, ensuring that there will be enough available for continuous use. The tray dispenser will need to be refilled every 15 minutes. This ensures that the machine doesn’t run out of trays, which can cause delays and decrease the overall time efficiency of the device.
To ensure proper functionality, it’s recommended that the trays be stacked and placed evenly into the machine. This not only helps with the flow of trays through the dispenser, but also prevents jams and other issues that can arise from uneven stacking.
By following these guidelines, users can ensure smooth and efficient tray dispensing, minimizing any downtime caused by errors.


Figure 4: Tray Dispenser

5

### 4.3 Pot Dropper

When using pot dropper system, the user can insert up to 300 pots manually into the uppermost section of the machine. Every 15 minutes, it is required for the user to refill the pot dropper to guarantee smooth operation of the device.
It is important to note that the pot dropper contains two sections, each of which can accommodate a certain number of pots. To optimize the efficiency of the machine and guarantee an even distribution of pots, it is recommended that users stack and place pots in both sections uniformly. Proper stacking and placement of pots into the machine helps to prevent any issues such as jamming, or other operational malfunctions.
By adhering to these guidelines, users can expect a reliable, efficient, and uninterrupted experience while using the pot dropper.


Figure 5: Pot Dropper

6

### 4.4 Verification System

The verification system will notify the user when there is a problem with the system. If there is a pot missing or out of place, an LED will light up, alerting the user that the system is not functioning as intended.

## 5 Troubleshooting and FAQs

### 5.1 What happens if trays get stuck?

If the trays get stuck, turn off the machine and remove them from the stack, and refill them evenly. Once they are in place, turn the machine on to run as normal.

### 5.2 What happens if pots get stuck?

If the pots get stuck, turn off the machine and remove them from the stack, and refill them evenly into both sections of the pot dropper. Once they are in place, turn the machine on to run as normal.

### 5.3 How many trays can the tray dropper hold?

The tray dropper can hold up to 30 trays, but it will need to be refilled every 15 minutes.

### 5.4 How many pots can the pot dropper hold?

The pot dropper can hold up to 300 pots, but it will need to be refilled every 15 minutes.

### 5.5 How will I know that all the pots have been placed correctly in the tray?

The verification subsystem will determine if all the pots have been placed correctly in the tray, outputting an LED and an error on the user interface when a pot is missing or out of place.

### 5.6 How do I refill the Pot-pulator with trays and pots?

When refilling pots and trays, ensure that the machine is turned off. 30 Trays and 300 pots can then be loaded evenly into their respective sections, the user can then turn on the machine for operation. The pot dropper has two sections, and the user can distribute them evenly between them.

7

### 5.7 How do I use the user interface of the Pot-pulator?

The user interface will display the current status of the machine. To learn more about the user interface and how to navigate it, please refer to the ”User Interface” section of the manual.

8

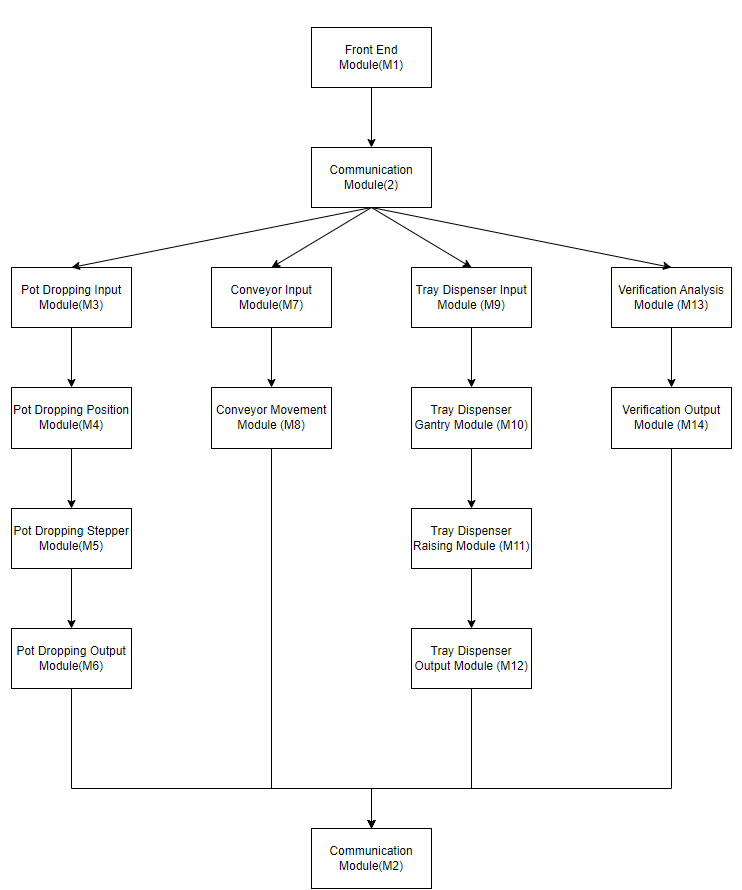
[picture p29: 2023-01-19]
docs/Design/SoftArchitecture/ModuleGuide.png

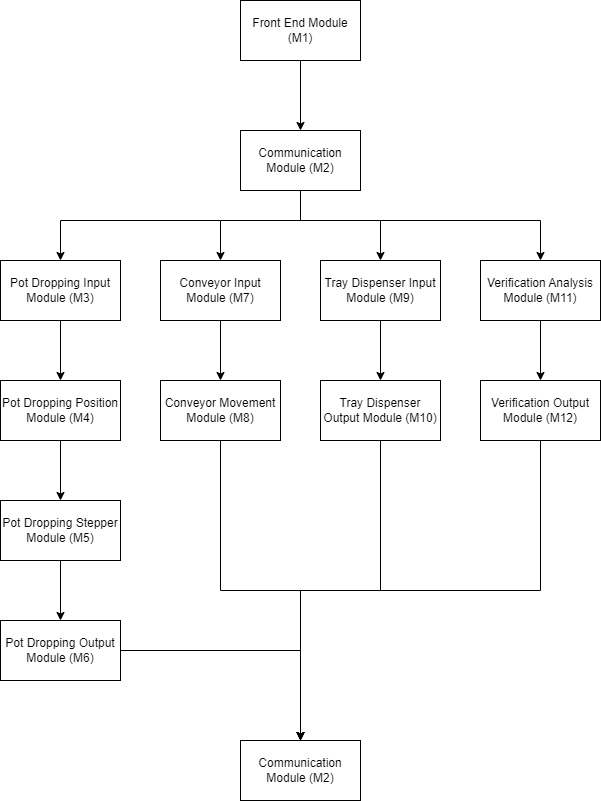
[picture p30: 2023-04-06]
docs/Design/SoftArchitecture/module_guide.png

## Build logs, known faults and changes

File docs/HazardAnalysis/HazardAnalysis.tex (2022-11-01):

\documentclass{article}

\usepackage{booktabs}
\usepackage{tabularx}
\usepackage{hyperref}
\usepackage[english]{babel}
\usepackage{enumitem}
\usepackage{pdflscape}
\usepackage{array}
\usepackage{longtable}
\hypersetup{
    colorlinks=true,       % false: boxed links; true: colored links
    linkcolor=red,          % color of internal links (change box color with linkbordercolor)
    citecolor=green,        % color of links to bibliography
    filecolor=magenta,      % color of file links
    urlcolor=cyan           % color of external links
}

\newcounter{srreqnum} %Likely change number
\newcommand{\lthesrreqnum}{LC\thesrreqnum}
\newcommand{\srref}[1]{SR\ref{#1}}

\title{Hazard Analysis The Nursery Poject}

\author{Aaron Billones, billonea\\Gillian Ford, fordg\\Juan Moncada, moncadaj\\Steven Ramundi, ramundis}

\date{October 19, 2022}

\input{../Comments}
\input{../Common}

\begin{document}

\maketitle
\thispagestyle{empty}

\pagenumbering{roman}

\begin{tabularx}{\textwidth}{p{3cm}p{4cm}X}
    \toprule {\bf Date} & {\bf Version} & {\bf Notes}\\
    \midrule
    2022-10-19 & Juan Moncada,& Initial release\\&Aaron Billones,\\&Steven Ramundi,\\&Gillian Ford \\
    
    \bottomrule
\end{tabularx}

~\newpage

\tableofcontents

~\newpage

\pagenumbering{arabic}

\section{Introduction}

\noindent This document is the hazard analysis of the Pot-Pulator. This machine will be built for Sheridan Nurseries, filling trays with pots, preparing them to be populated with soil and seeds, to reduce the manual labour of the workers at the farm. The hazard analysis will consider each part of the Pot-Pulator, including the respective tray and pot droppers, the sensor verification section, and the conveyor belt. 
\\

\noindent The definition of a hazard used in this document is any issue or property in the Pot-Pulator that will cause a risk to the ideal result of the system. In this system, most hazards will be concerning safety of the workers collecting the trays at the end of the conveyor, and the effectiveness of the verification system. 
\\

\noindent This document will include the Scope and Purpose of Hazard Analysis, System Boundaries and Components, Failure Mode and Effect Analysis, and Safety \& Security Requirements.  

\section{Scope and Purpose of Hazard Analysis}

\noindent The scope of this document is to identify the components of the Pot-Pulator that could have harmful consequences to the users or the results and reduce each risk to a level where the overall system will be safe and acceptable. 
\\

\noindent Hazards will be analyzed based on research of similar systems, and any specific hazards occurring throughout the development process of the machine. 

\section{System Boundaries and Components}

The hazard analysis will be conducted based on the Pot-Pulator, which is restricted to the components below. 

\begin{enumerate}
    \item Conveyor belt
    \item Tray allocation
    \item Pot dropping
    \item Verification system
\end{enumerate}

\noindent The hazard analysis will be based on these critical elements of the system. The system boundary includes a conveyor belt moving the system along, tray allocation to place the trays on the conveyor, a pot dropper to place the pots into the trays, and a verification system to confirm the correct placement of the components. 
\clearpage
\noindent The conveyor belt will be controlled by a sensor based on the other components. At the end of the process, the conveyor belt will bring the completed trays to the end of the line, to be collected by a worker. This will all be accounted for in the hazard analysis. 

\section{Critical Assumptions}

It is assumed there will be no damage to the system by water, pressure, or similar external factors, considering the machine will only be used within the nursery in ideal conditions.  

\newpage
\begin{landscape}
\section{Failure Mode and Effect Analysis (FMEA)}

\begin{center}
    
    \begin{longtable}{|l|  p{3cm}  p{4cm}  p{3cm}  p{4cm}  p{2cm}  p{1cm}|}
        \caption{FMEA}\\
        \label{tab:Table1}\\
        \hline
        Component&
        Failure Mode&
        Effect of Failure&
        Cause of Failure &
        Recommended Action &
        SR&
        Ref \\
        \hline
        \begin{centering}
        Tray Dispensing
        \end{centering} &
        Tray is not dispensed & 
        Machine is unable to continue operation, tray may be damaged & 
        \begin{enumerate}[label=(\alph*)]
            \item Tray stack software/hardware failure
            \item Tray dispenser software/hardware failure 
            \item Parts failure 
        \end{enumerate} &
        \begin{enumerate}[label=(\alph*)]
            \item  Sensor will recognize if tray has not been dispensed, error message will be displayed and operator will be notified.
            \item  Refer to H1-1a
            \item Refer to H1-1a
        \end{enumerate}&
        \begin{enumerate}[label=(\alph*)]
            \item SR4, SR7, SR9
            \item SR4, SR7, SR9
            \item SR4, SR7, SR9
        \end{enumerate}&
        H1-1\\
 
         &
        Trays placed incorrectly on conveyor&
        Tray is unable to move forward on conveyor, pot dispenser is unable to place pots correctly. May damage pots/trays&
        Tray dispenser software/hardware failure&
        Guiding rods will be placed on the conveyor to centre trays into correct position. If trays are unable to move forward, error message will be displayed and operator will be notified.&
        SR4, SR7, SR9&
        H1-2\\

        &
        Trays dispensed are stacked, 2+ trays dispensed at once&
        Tray storage becomes out of sync with pot storage, may damage pots/trays&
        \begin{enumerate}[label=(\alph*)]
            \item Parts failure 
            \item Trays loaded incorrectly
        \end{enumerate} &
        \begin{enumerate}[label=(\alph*)]
            \item Sensor will recognize if multiple trays have been dispensed, error message will be displayed and operator will be notified
            \item Operator will be trained to properly load trays into machine"	
        \end{enumerate}&
        \begin{enumerate}[label=(\alph*)]
            \item SR4, SR7, SR9
            \item SR17
        \end{enumerate}&
        H1-3\\
        &
        Tray dispenser damages tray&	
        Tray is unable to hold pots and be sent for distribution (will depend on severity of damage to tray)&
        Quality issue in trays&
        Operator will be trained to perform 60 second visual check of Pot-pulator, trays, and pots before each refill to note and eliminate trays with any noticeable defects&		
        SR17&
        H1-4\\
        \hline
        Pot Dispensing&
        Pots are not dispensed&
        Tray will be dispensed empty&
        Software/hardware failure&
        Sensor post pot dispensing will sense that the tray has not been populated, error message will be displayed and operator will be notified&		
        SR4, SR7, SR10&
        H2-1\\

        &
        Pots dispensed are not flush with tray openings&
        Pots will be damaged by Pot-pulator or soil filling machine&
        \begin{enumerate}[label=(\alph*)]
            \item Software/hardware failure
            \item Quality issue in pots
            \item Quality issue in trays
        \end{enumerate}&
        \begin{enumerate}[label=(\alph*)]
            \item Sensor will recognize that pot is not flush with tray opening, error message will be displayed and operator will be notified
            \item Operator will be trained to perform 60 second visual check of Pot-pulator, trays, and pots before each refill to note and eliminate pots with any noticeable defects
            \item Refer to H1-4
        \end{enumerate}&
        \begin{enumerate}[label=(\alph*)]
            \item SR4, SR7, SR10
            \item SR17
            \item SR17
        \end{enumerate}&
        
        H2-2\\

        &
        Pots dispensed when tray is not present&
        Pot storage becomes out of sync with tray storage&
        Software/hardware failure&
        Sensor will recognize if pots are dispensed without tray present, error message will be displayed and operator will be notified&
        SR4, SR7, SR10&
        H2-3\\

        &
        Pots dispensed are stacked&
        Pots will be damaged by Pot-pulator or soil filling machine&
        \begin{enumerate}[label=(\alph*)]
            \item Parts failure
            \item Pots loaded incorrectly
        \end{enumerate}&
        \begin{enumerate}[label=(\alph*)]
            \item Sensor will recognize if multiple pots have been dispensed, error message will be displayed and operator will be notified
            \item Operator will be trained to properly load pots into machine
        \end{enumerate}&
        \begin{enumerate}[label=(\alph*)]
            \item SR4, SR7, SR10
            \item SR17
        \end{enumerate}&
        
        H2-4\\

        &
        Pot dispenser damages pots&
        Pots are unable to be filled with soil and sent for distribution&
        Quality issue in pots&
        Refer to H2-2b&
        SR17&
        H2-5\\
        \hline
        Conveyor&
        Conveyor does not move&
        Tray is unable to move to soil filling machine, trays may be damaged&
        \begin{enumerate}[label=(\alph*)]
            \item Software/hardware failure
            \item Parts failure
        \end{enumerate}&
        \begin{enumerate}[label=(\alph*)]
            \item Sensor will recognize if conveyor is not moving for extended period of time, error message will be displayed and operator will be notified
            \item Operator will be trained to perform 60 second visual check of Pot-pulator before pots and trays refill to note any damage to conveyor or belt wear
        \end{enumerate}&
        \begin{enumerate}[label=(\alph*)]
            \item SR4, SR7, SR11
            \item SR17
        \end{enumerate}&
        H3-1\\
        &
        Conveyor does not stop when it is meant to&
        Pots are unable to be placed properly in trays, pots and/or trays may be damaged&
        Software/hardware failure&
        If tray is in view of pot dispenser, refer to H2-2a. If tray is not in view of pot dispenser, refer to H2-3&
        SR10&
        H3-2\\
        &
        Trays slide on conveyor when conveyor is accelerating/deccelerating&
        Pots are unable to be placed properly in trays, trays may be damaged&
        \begin{enumerate}[label=(\alph*)]
            \item Software/hardware failure
            \item Belt failure
        \end{enumerate}&
        \begin{enumerate}[label=(\alph*)]
            \item Sensor will recognize if conveyor is accelerating/deccelerating at a magnitude greater than specified, error message will be displayed and operator will be notified
            \item Refer to H3-1b
        \end{enumerate}&
        \begin{enumerate}[label=(\alph*)]
            \item SR4, SR5, SR7, SR11
            \item SR17
        \end{enumerate}&
        H3-3\\

        &
        Conveyor is unable to reach desired speed&
        Machine is unable to meet production standards&
        \begin{enumerate}[label=(\alph*)]
            \item Software/hardware failure
            \item Parts failure
        \end{enumerate}&
        \begin{enumerate}[label=(\alph*)]
            \item  Sensor will recognize if conveyor is not reaching desired speed for extended period of time, error message will be displayed and operator will be notified
            \item Refer to H3-1b
        \end{enumerate}&
        \begin{enumerate}[label=(\alph*)]
            \item SR4. SR7, SR11
            \item SR17
        \end{enumerate}&
        H3-4\\

        \hline

        Verification System&
        Tray with less than 10 pots passses through verification system&
        Trays are unable to be sent for ditribution, trays are wasted, pot and tray storage will become out of sync&
        \begin{enumerate}[label=(\alph*)]
            \item Software/hardware failure
            \item Verification sensors are obstructed/damaged
        \end{enumerate}&
        \begin{enumerate}[label=(\alph*)]
            \item Soil machine operator will be inspecting all trays leaving the soil machine. If a tray with less than 10 pots is identified, soil machine operator will be trained to manually stop Pot-pulator
            \item Operator will be trained to perform 60 second visual check of Pot-pulator before pots and trays refill to note any obstructions/damage to sensors
        \end{enumerate}&
        \begin{enumerate}[label=(\alph*)]
            \item SR12
            \item SR17
        \end{enumerate}&
        H4-1\\

        &
        Verification system does not stop machine process when required to&
        Trays are unable to be sent for distribution, may cause damage to trays&
        \begin{enumerate}[label=(\alph*)]
            \item Software/hardware failure
            \item Verification sensors are obstructed/damaged
        \end{enumerate}&
        \begin{enumerate}[label=(\alph*)]
            \item Refer to H4-1a
            \item Refer to H4-1b
        \end{enumerate}&
        \begin{enumerate}[label=(\alph*)]
            \item SR12
            \item SR17
        \end{enumerate}&
        H4-2\\

        \hline

        General&
        Person comes into contact with moving parts of machine&
        Potential risk of serious injury or death&
        \begin{enumerate}[label=(\alph*)]
            \item Operator wearing loose clothing or jewellery
            \item Operator places hand in machine during operation
        \end{enumerate}&
        \begin{enumerate}[label=(\alph*)]
            \item Moving parts will be covered and protected. Emergency cut off switch will be implemented to cut all power to Pot-pulator. Physical emergency instructions and labels will be placed on the device. Operators will complete safety training before operating the Pot-pulator
            \item Refer to H5-1a
        \end{enumerate}&
        \begin{enumerate}[label=(\alph*)]
            \item SR3, SR6, SR15, SR17
            \item SR3, SR6, SR15, SR17
        \end{enumerate}&
        H5-1\\

        &
        Person comes into contact with electronics of machine&
        Potential risk of serious injury or death&
        Operator makes accidental contact with electrical wiring or electronics of machine&
        Electrical equipment and electronics will be covered and protected. Emergency cut off switch will be implemented to cut all power to Pot-pulator. Physical emergency instructions and labels will be placed on the device. Operators will complete electrical safety training before operating the Pot-pulator&
        SR1, SR2, SR6, SR8, SR15, SR17&
        H5-2\\

        &
        Machine is subject to unexpected external force&
        Potential risk of injury to operator, may damage machine components, pots, or trays, may interrupt machine operation&
        Accidental bump from person/equipment passing by machine&
        Pot-pulator base will be reinforced to ensure it is able to withstand a reasonable unexpected external force&
        SR13&
        H5-3\\

    \cline{2-7}
    \hline

    % Conveyor & Failure Mode & Effect of Failure & Cause of failure & Recomended action \\
    % \hline
    % Pot Dispensing & Failure Mode & Effect of Failure & Cause of failure & Recomended action  \\
    % \hline
    % Verification & Failure Mode & Effect of Failure & Cause of failure & Recomended action  \\
    % \hline
    \end{longtable}
\end{center}
\end{landscape}

\newpage

\section{Safety and Security Requirements}

\subsection{Existing Requirements}
The following are listed as non-functional requirements that can be found in 
the Software Requirements Specification (SRS) document (reference in square brackets).
These requirements are related to the safety and security of the system which are necessary during operation.
\\
\begin{itemize}
    \item[SR\refstepcounter{srreqnum}\thesrreqnum \label{SR1}:]
    All electrical equipment and electronics must be well covered and protected. The user must not have access to equipment. [NFR1]
    \item[SR\refstepcounter{srreqnum}\thesrreqnum \label{SR2}:]
    All wiring must be tucked away and not accessible to avoid potential electrical failure. [NFR2]
    \item[SR\refstepcounter{srreqnum}\thesrreqnum \label{SR3}:]
    All moving parts must be covered and protected. Moving parts should be covered to protect both the mechanism and the safety of the operator. [NFR3]
    \item[SR\refstepcounter{srreqnum}\thesrreqnum \label{SR4}:]
    System must have both audible and visible signal outputs for each system status. [NFR7]
    \item[SR\refstepcounter{srreqnum}\thesrreqnum \label{SR5}:]
    Conveyor system must not accelerate in a manner that would shift the position of 
    the tray on the conveyor belt. A shift in the position of the tray could result in a misalignment and potential error. [NFR8]
    \item[SR\refstepcounter{srreqnum}\thesrreqnum \label{SR6}:]
    System must have emergency cut off. In case of any emergency, this will trip off all power to the Pot-Pulator. [NFR11]
    \item[SR\refstepcounter{srreqnum}\thesrreqnum \label{SR7}:]
    System must be able to locate and identify failures within each independent subsystem. [NFR12]
    \item[SR\refstepcounter{srreqnum}\thesrreqnum \label{SR8}:]
    System must follow electronic component safety requirements. [NFR25]
    \item[SR\refstepcounter{srreqnum}\thesrreqnum \label{SR9}:]
    The tray dispenser must stop when an error arises (verification failed, pot dispenser malfunction/empty, conveyor malfunction). [TDR6]
    \item[SR\refstepcounter{srreqnum}\thesrreqnum \label{SR10}:]
    The pot dispenser must stop when an error arises (verification failed, tray dispenser malfunction/empty, conveyor malfunction). [PDR7]
    \item[SR\refstepcounter{srreqnum}\thesrreqnum \label{SR11}:]
    The conveyor must stop when an error arises (verification failed, pot dispenser malfunction/empty, tray dispenser malfunction/empty). [CR5]
    \item[SR\refstepcounter{srreqnum}\thesrreqnum \label{SR12}:]
    {The verification must notify all other systems if verification fails, such that $n_{traysout}\neq1\ or\ n_{potsout}\neq10$ [VR2]}

  \end{itemize}

\subsection{New Requirements}
The following are listed as non-functional requirements related to 
safety and security of the system that were formulated upon performing 
hazard analysis. Reference to the new requirements in the SRS are shown in square brackets.\\

\begin{itemize}
    \item[SR\refstepcounter{srreqnum}\thesrreqnum \label{SR13}:]
    System must be able to withstand a sufficient physical force to keep from falling over. [NFR26]
    \item[SR\refstepcounter{srreqnum}\thesrreqnum \label{SR14}:]
    System must obtain a user login system or physical start key. [NFR27]
    \item[SR\refstepcounter{srreqnum}\thesrreqnum \label{SR15}:]
    Clear physical emergency instructions and labels located on the device. [NFR28]
    \item[SR\refstepcounter{srreqnum}\thesrreqnum \label{SR16}:]
    System must have surge protection. [NFR29]
    \item[SR\refstepcounter{srreqnum}\thesrreqnum \label{SR17}:]
    Operators must be properly trained in general safety, electronic safety, and system operation. [NFR30]
\end{itemize}

\section{Roadmap}

There were some new non-functional requirements (safety and security) discovered, 
after performing hazard analysis on the system. The safety and security requirements 
that will be implemented in the future beyond the timeline of the capstone are SR7, 
SR14, and SR16. These requirements will be apart of a future implementation due to 
time-related and financial reasons. The remaining non-functional requirements related 
to safety and security will be implemented within the timeline the capstone project.

\section{List of Tables}
\autoref{tab:Table1} : FMEA

\end{document}

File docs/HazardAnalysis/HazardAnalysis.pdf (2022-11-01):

# Hazard Analysis The Nursery Poject

Aaron Billones, billonea
Gillian Ford, fordg
Juan Moncada, moncadaj
Steven Ramundi, ramundis

October 19, 2022

Date | Version | Notes
2022-10-19 | Juan Moncada, | Initial release
| Aaron Billones, Steven Ramundi, Gillian Ford

## Contents

1 Introduction | 1
2 Scope and Purpose of Hazard Analysis | 1
3 System Boundaries and Components | 1
4 Critical Assumptions | 2
5 Failure Mode and Effect Analysis (FMEA) | 3
6 Safety and Security Requirements | 13
7 Roadmap | 14
8 List of Tables | 14

ii

## 1 Introduction

This document is the hazard analysis of the Pot-Pulator. This machine will be built for Sheridan Nurseries, filling trays with pots, preparing them to be populated with soil and seeds, to reduce the manual labour of the workers at the farm. The hazard analysis will consider each part of the Pot-Pulator, including the respective tray and pot droppers, the sensor verification section, and the conveyor belt.

The definition of a hazard used in this document is any issue or property in the Pot-Pulator that will cause a risk to the ideal result of the system. In this system, most hazards will be concerning safety of the workers collecting the trays at the end of the conveyor, and the effectiveness of the verification system.

This document will include the Scope and Purpose of Hazard Analysis, System Boundaries and Components, Failure Mode and Effect Analysis, and Safety & Security Requirements.

## 2 Scope and Purpose of Hazard Analysis

The scope of this document is to identify the components of the Pot-Pulator that could have harmful consequences to the users or the results and reduce each risk to a level where the overall system will be safe and acceptable.

Hazards will be analyzed based on research of similar systems, and any specific hazards occurring throughout the development process of the machine.

## 3 System Boundaries and Components

The hazard analysis will be conducted based on the Pot-Pulator, which is restricted to the components below.

1. Conveyor belt
2. Tray allocation
3. Pot dropping
4. Verification system

The hazard analysis will be based on these critical elements of the system. The system boundary includes a conveyor belt moving the system along, tray allocation to place the trays on the conveyor, a pot dropper to place the pots into the trays, and a verification system to confirm the correct placement of the components.

1

The conveyor belt will be controlled by a sensor based on the other components. At the end of the process, the conveyor belt will bring the completed trays to the end of the line, to be collected by a worker. This will all be accounted for in the hazard analysis.

## 4 Critical Assumptions

It is assumed there will be no damage to the system by water, pressure, or similar external factors, considering the machine will only be used within the nursery in ideal conditions.

2

## 5 Failure Mode and Effect Analysis (FMEA)

Table 1: FMEA

Component | Failure Mode | Effect of Failure | Cause of Failure | Recommended Action | SR | Ref
Tray Dispensing | Tray is not dis-
| pensed | Machine is unable to con- tinue operation, tray may
| | be damaged
(a) Tray
stack | soft-
| | | ware/hardware
| | | failure
(b) Tray | dis-
penser | soft-
| | | ware/hardware
| | | failure
(c) Parts failure
(a) Sensor will recognize if tray has not
been dispensed, error message will be
displayed and operator will be notified.
(b) Refer to H1-1a
(c) Refer to H1-1a
(a) SR4,
SR7,
SR9
(b) SR4,
SR7,
SR9
(c) SR4,
SR7,
SR9

H1-1

Trays placed incor-

rectly on conveyor | Tray is unable to move for- ward on conveyor, pot dis-
| penser is unable to place pots correctly. May dam- age pots/trays

Tray dispenser software/hardware fail-

ure | Guiding | rods | will | be placed on the conveyor to centre trays into correct
position. | If trays are
unable to move forward,
error message will be
displayed and operator
will be notified.

SR4, SR7,
SR9

H1-2

3

Trays dispensed are
stacked, 2+ trays
dispensed at once

Tray storage becomes out
of sync with pot storage,
may damage pots/trays | (a) Parts failure
(b) Trays loaded
incorrectly
(a) Sensor | will | rec-
ognize if multiple
trays | have | been
dispensed, | error
message will be displayed and operator
will be notified
(b) Operator | will | be
trained to properly
load trays into machine”
(a) SR4,
SR7,
SR9
(b) SR17

H1-3

Tray dispenser
damages tray

Tray is unable to hold pots and be sent for distribution (will depend on severity of damage to tray)

Quality | issue | in
trays

Operator will be trained
to perform 60 second visual check of Pot-pulator, trays, and pots before
each refill to note and
eliminate trays with any
noticeable defects
SR17 | H1-4
Pot Dispensing | Pots are not dis-
pensed | Tray will be dispensed empty | Software/hardware failure | Sensor post pot dispens- ing will sense that the tray
| | | has not been populated, error message will be dis- played and operator will be notified
SR4, | SR7,
SR10

H2-1

4

Pots dispensed are
not flush with tray
openings

Pots will be damaged by
Pot-pulator or soil filling
machine | (a)
Software/hardware
failure
(b) Quality issue
in pots
(c) Quality issue
in trays
(a) Sensor will recognize
that pot is not flush
with tray opening,
error message will be
displayed and operator will be notified
(b) Operator | will | be
trained | to | per-
form | 60 | second
visual | check | of
Pot-pulator, | trays,
and | pots | before
each refill to note
and eliminate pots
with any noticeable
defects
(c) Refer to H1-4
(a) SR4,
SR7,
SR10
(b) SR17
(c) SR17

H2-2

Pots dispensed
when tray is not
present

Pot storage becomes out
of sync with tray storage

Software/hardware
failure

Sensor will recognize if
pots are dispensed without tray present, error
message will be displayed
and operator will be notified

SR4, SR7,
SR10

H2-3

5

Pots dispensed are
stacked

Pots will be damaged by
Pot-pulator or soil filling
machine | (a) Parts failure
(b) Pots | loaded
incorrectly
(a) Sensor will recognize
if multiple pots have
been dispensed, error message will be
displayed and operator will be notified
(b) Operator | will | be
trained to properly
load pots into machine
(a) SR4,
SR7,
SR10
(b) SR17

H2-4

Pot dispenser dam-

ages pots | Pots are unable to be filled with soil and sent for dis-
tribution | Quality | issue | in pots
6
Refer to H2-2b | SR17 | H2-5

Conveyor | Conveyor does not
move

Tray is unable to move to
soil filling machine, trays
may be damaged | (a) Software/hardware

failure

(b) Parts failure
(a) Sensor will recognize
if conveyor is not
moving for extended
period of time, error
message will be displayed and operator
will be notified
(b) Operator | will | be
trained to perform
60 | second | visual
check of Pot-pulator
before | pots | and
trays refill to note
any damage to conveyor or belt wear
(a) SR4,
SR7,
SR11
(b) SR17

H3-1

Conveyor does not
stop when it is
meant to

Pots are unable to be
placed properly in trays,
pots and/or trays may be
damaged

Software/hardware
failure

If tray is in view of pot dispenser, refer to H2-2a. If tray is not in view of pot dispenser, refer to H2-3

SR10 | H3-2

7

Trays slide on conveyor when conveyor is accelerat-

ing/deccelerating | Pots are unable to be placed properly in trays, trays may be damaged | (a) Software/hardware failure
(b) Belt failure
(a) Sensor | will | rec-
ognize | if | con-
veyor is accelerating/deccelerating at
a magnitude greater
than specified, error
message will be displayed and operator
will be notified
(b) Refer to H3-1b
(a) SR4,
SR5,
SR7,
SR11
(b) SR17

H3-3

Conveyor is unable
to | reach | desired
speed

Machine is unable to meet
production standards | (a)

Software/hardware
failure
(b) Parts failure
(a) Sensor will recognize if conveyor is
not reaching desired
speed for extended
period of time, error
message will be displayed and operator
will be notified
(b) Refer to H3-1b
(a) SR4.
SR7,
SR11
(b) SR17

8

H3-4

Verification System | Tray with less than
10 | pots | passses
through | verifica-
tion system

Trays are unable to be
sent for ditribution, trays are wasted, pot and tray
storage will become out of sync

(a)
Software/hardware
failure
(b) Verification
sensors
are | ob-
structed/damaged
(a) Soil machine operator will be inspecting all trays leaving
the soil machine. If
a tray with less than
10 pots is identified,
soil machine operator will be trained to
manually stop Pot-pulator
(b) Operator | will | be
trained | to | per-
form | 60 | second
visual check of Pot-pulator before pots
and trays refill to
note any obstructions/damage to
sensors
(a) SR12
(b) SR17

H4-1

9

Verification system
does not stop machine process when
required to

Trays are unable to be
sent for distribution, may
cause damage to trays | (a) Software/hardware

failure

(b) Verification
sensors
are | ob-
structed/damaged
(a) Refer to H4-1a
(b) Refer to H4-1b
(a) SR12
(b) SR17

H4-2

10

General | Person comes into
contact with moving parts of machine

Potential risk of serious in-
jury or death | (a) Operator

wearing loose
clothing or
jewellery
(b) Operator
places | hand
in | machine
during operation
(a) Moving parts will
be covered and protected. Emergency
cut off switch will
be implemented to
cut all power to
Pot-pulator. Physical emergency instructions and labels
will be placed on
the device. Operators will complete
safety training before operating the
Pot-pulator
(b) Refer to H5-1a
(a) SR3,
SR6,
SR15,
SR17
(b) SR3,
SR6,
SR15,
SR17

H5-1

11

Person comes into
contact with electronics of machine

Potential risk of serious in-

jury or death | Operator | makes accidental contact
| with | electrical
wiring or electronics of machine

Electrical equipment and
electronics will be covered and protected. Emergency cut off switch will
be implemented to cut
all power to Pot-pulator.
Physical emergency instructions and labels will be placed on the device.
Operators will complete
electrical safety training before operating the Pot-pulator
SR1, | SR2,
SR6, | SR8,
SR15, SR17

H5-2

Machine is subject
to unexpected external force

Potential risk of injury
to operator, may damage machine components,
pots, or trays, may interrupt machine operation

Accidental
bump | from | per-
son/equipment
passing by machine

Pot-pulator base will be
reinforced to ensure it is able to withstand a reasonable unexpected external force

12

SR13 | H5-3

## 6 Safety and Security Requirements

### 6.1 Existing Requirements

The following are listed as non-functional requirements that can be found in the Software Requirements Specification (SRS) document (reference in square brackets). These requirements are related to the safety and security of the system which are necessary during operation.

SR1: All electrical equipment and electronics must be well covered and protected. The user must not have access to equipment. [NFR1]

SR2: All wiring must be tucked away and not accessible to avoid potential electrical failure. [NFR2]

SR3: All moving parts must be covered and protected. Moving parts should be covered to protect both the mechanism and the safety of the operator. [NFR3]

SR4: System must have both audible and visible signal outputs for each system status. [NFR7]

SR5: Conveyor system must not accelerate in a manner that would shift the position of the tray on the conveyor belt. A shift in the position of the tray could result in a misalignment and potential error. [NFR8]

SR6: System must have emergency cut off. In case of any emergency, this will trip off all power to the Pot-Pulator. [NFR11]

SR7: System must be able to locate and identify failures within each independent subsystem. [NFR12]

SR8: System must follow electronic component safety requirements. [NFR25]

SR9: The tray dispenser must stop when an error arises (verification failed, pot dispenser malfunction/empty, conveyor malfunction). [TDR6]

SR10: The pot dispenser must stop when an error arises (verification failed, tray dispenser malfunction/empty, conveyor malfunction). [PDR7]

SR11: The conveyor must stop when an error arises (verification failed, pot dispenser malfunction/empty, tray dispenser malfunction/empty). [CR5]

SR12: The verification must notify all other systems if verification fails, such that

ntraysout ̸= 1 or npotsout ̸= 10 [VR2]

13

### 6.2 New Requirements

The following are listed as non-functional requirements related to safety and security of the system that were formulated upon performing hazard analysis. Reference to the new requirements in the SRS are shown in square brackets.

SR13: System must be able to withstand a sufficient physical force to keep from falling over. [NFR26]

SR14: System must obtain a user login system or physical start key. [NFR27]

SR15: Clear physical emergency instructions and labels located on the device. [NFR28]

SR16: System must have surge protection. [NFR29]

SR17: Operators must be properly trained in general safety, electronic safety, and system operation. [NFR30]

## 7 Roadmap

There were some new non-functional requirements (safety and security) discovered, after performing hazard analysis on the system. The safety and security requirements that will be implemented in the future beyond the timeline of the capstone are SR7, SR14, and SR16. These requirements will be apart of a future implementation due to time-related and financial reasons. The remaining non-functional requirements related to safety and security will be implemented within the timeline the capstone project.

## 8 List of Tables

Table 1 : FMEA

14

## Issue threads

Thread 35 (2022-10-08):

Team_21_Review

purefisher, 2022-10-08:

purefisher, 2022-10-08:
SRS Review Team 24 – The Pot-Pulator

Issues with The Nursery Project SRS:
1. Listed Conveyor Speed as a monitored variable. The speed should just be specified in the software by how much voltage you are giving your motor to get a specific rpm. Should be easy to calculate and control this in software via your control variable of Motor Speeds.
2. Listing both Tray/Pot Height and Weight to verify the number of them in the stack. Is this redundancy to measure the same thing important?
3. Is System State really a monitored variable? Sounds more like a state you'll reach in an FSM diagram based on your other monitored variables.
4. How often should the system be routinely maintained and cleaned to ensure accurate operation?
5. Pot material should be considered. If the pots are made of clay this would need to be considered as it has a higher chance of breaking. If the pots are all plastic, then this assumption should be made.

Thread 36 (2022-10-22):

Team 20 HA Review: FMEA H2-4b Recommended Action

kelhuynh, 2022-10-22:
The recommended action pertains more to the operator (user) rather than the system. The recommended action should be more about how the system should react to and detect pots being improperly loaded. For example, the pots being improperly loaded could potentially be detected by the system through the use of sensors in which it could then provide a warning to the operator so that corrective action can be taken.

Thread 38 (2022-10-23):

Team 20 HA Review: Sensor Component

zhul49, 2022-10-23:
As sensors are not listed as a Critical Assumption, and plays a large role in recognizing many of the failures that might occur, adding a sensor component might be important to check and verify they are working properly. This can be done, for example, with a weekly inspection by the operator (user) or an automated test run to ensure that all failures will be detected for safety.

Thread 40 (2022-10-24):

Team 20 HA Review: Recommended Action for Critical Assumptions

mengz17, 2022-10-24:
It would be better if more details were provided in the Critical Assumptions section. For example, why these assumptions (water and pressure) are made, under what circumstances could these hazards happen, or what failures could these hazards cause. In this way, readers can have a better understanding of the intensions behind these assumptions.

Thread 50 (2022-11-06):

Team 19 VnV Review

rangaran, 2022-11-06:
Hi guys, I noticed when you were talking about testing, you mentioned two types of testing for some test cases. In such cases, it is important to demarcate how these two types of testing will play a role in the “how the test will be performed section”. Say for instance, dynamic with manual testing should not only talk about how the system will interact with the input but also talk about the test in the context of black box or white box testing.

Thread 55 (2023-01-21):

Team 18 Review: MG - Unlikely Changes

Niu0351, 2023-01-21:
One potential issue in the 'Unlikely Changes' module is the use of a specific control board (STM32F421i-DISC1) as the main brain of the system. This may limit the flexibility of the design in the future and make it difficult to adapt to potential changes.

For example, if in the future the team wants to add new features or capabilities to the system that are not supported by the STM32F421i-DISC1, they would have to replace the entire control board, which could be a costly and time-consuming process. Alternatively, if a new control board that is more powerful or has more features becomes available, the team would have to replace the STM32F421i-DISC1 with the new one. This could limit the ability to upgrade the system in the future.

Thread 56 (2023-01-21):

Team 18 Review: MIS - Need More Information

senni0418, 2023-01-21:
For the local function, some details are missing, for example,
localFunction():
transition:
output:

For the environment variables, for example, on page 4, environment variable stepper_position, coil_1a, coil_1b... Adding some comments may help the reader better understand the content.

For the state variables, for example, on page 6, the state variables are declared but the state variables are not initialized or updated by functions in this module, which is weird from the software point of perspective.

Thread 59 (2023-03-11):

Team 17 Review: VnVReport - Missing Navigation References

LilVegedog, 2023-03-11:
As specified in the rubric, for the readers to be easier to navigate through the document, navigation references should be provided. I think it would be better to add navigation references for each of the tests in the traceability tables to requirement and modules so that the reader can check what a test is about by simply clicking the test name in the tables instead of scrolling up and down throughout the report document.

@samm82

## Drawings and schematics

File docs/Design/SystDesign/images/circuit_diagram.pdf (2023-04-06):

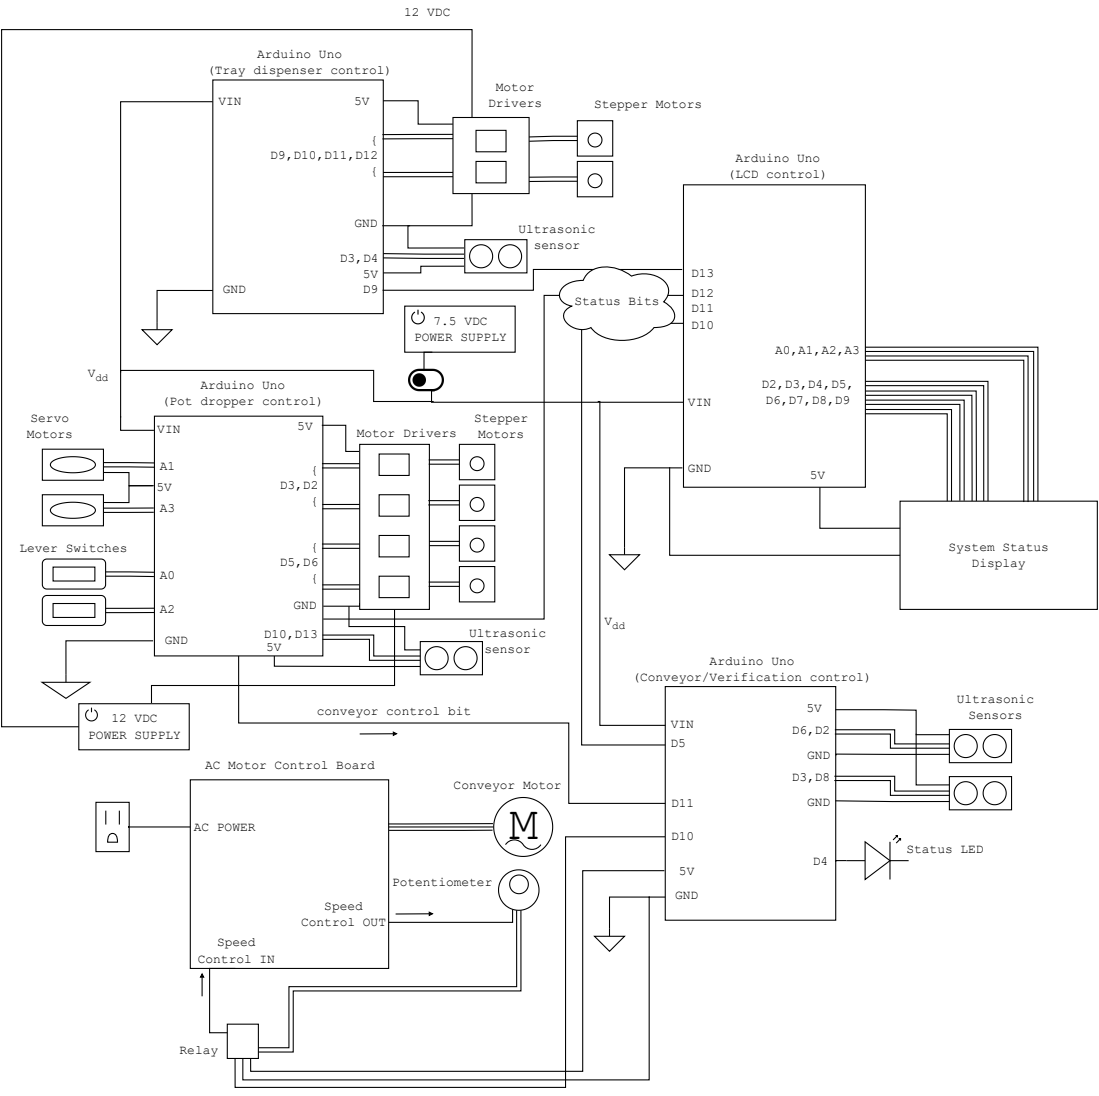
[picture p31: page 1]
AC POWER; Speed Control OUT; Speed Control IN; GND; VIN; Conveyor Motor; Relay; Potentiometer; Stepper Motors; Arduino Uno; Motor; Drivers; Ultrasonic Sensors; Status LED; Motor Drivers; Ultrasonic sensor; Servo Motors; Lever Switches; System Status Display; Arduino Uno (LCD control); Status Bits; 7.5 VDC POWER SUPPLY; Vdd; 12 VDC POWER SUPPLY; 12 VDC

(Tray dispenser control)

Arduino Uno
(Pot dropper control)

(Conveyor/Verification control)

conveyor control bit

AC Motor Control Board

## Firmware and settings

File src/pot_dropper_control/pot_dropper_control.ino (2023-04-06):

#include <Servo.h>
#define trigPin 10
#define echoPin 13
#define LIMIT_SWITCH_PIN_L A0
#define LIMIT_SWITCH_PIN_R A2  
#define servoPin1 A1
#define servoPin2 A3
#define errorPin A4
#define conveyorPin 11

const int stepPin1 = 2; 
const int dirPin1 =3; 
const int stepPin2 = 5; 
const int dirPin2 = 6;

Servo Servo1; 
Servo Servo2;

void setup() {
  // put your setup code here, to run once:
  Serial.begin (9600);
  pinMode(LIMIT_SWITCH_PIN_L, INPUT);
  Servo1.attach(servoPin1); 
  pinMode(LIMIT_SWITCH_PIN_R, INPUT);
  Servo2.attach(servoPin2); 

  pinMode(trigPin, OUTPUT);
  pinMode(echoPin, INPUT);
  pinMode(conveyorPin, OUTPUT);//pin to control start/stop of conveyor
  pinMode(stepPin1,OUTPUT); 
  pinMode(dirPin1,OUTPUT);
  pinMode(stepPin2,OUTPUT); 
  pinMode(dirPin2,OUTPUT);
  pinMode(errorPin, OUTPUT); //pin to output error to screen
  Servo1.write(0); //servo down
  Servo2.write(90); //servo down
  digitalWrite(errorPin, LOW);
}

void loop() {
  // put your main code here, to run repeatedly:

  digitalWrite(conveyorPin, LOW); // start conveyor command

  //sensor control
  float duration, distance;
  digitalWrite(trigPin, LOW); 
  delayMicroseconds(2);
 
  digitalWrite(trigPin, HIGH);
  delayMicroseconds(10);
  digitalWrite(trigPin, LOW);
  
  duration = pulseIn(echoPin, HIGH);
  distance = (duration / 2) * 0.0344;
  Serial.print("Distance = ");
  Serial.print(distance);
  Serial.println(" cm");
  delay(10);

  //determines if tray is not below pot dropper and lowers arm switches
  if(distance >20 && distance <50){
    delay(850);
    Servo1.write(0);
    Servo2.write(90);
  }
    else digitalWrite(errorPin, HIGH); //send error message to screen

  //determine if arm switches are pressed by tray, begin pot dropping sequence
  if (digitalRead(LIMIT_SWITCH_PIN_L) == HIGH && digitalRead(LIMIT_SWITCH_PIN_R) == HIGH){
    digitalWrite(11, HIGH);
    delay(500);
    Servo1.write(90); //servo up
    Servo2.write(0); //servo up
    delay(500);
    //run stepper rotation for 5 sequences
    for(int i=0;i<5;i++){
      digitalWrite(11, HIGH); //stop conveyor command
      digitalWrite(dirPin1,HIGH); //
      digitalWrite(dirPin2,HIGH);
        //full rotation of stepper motors 
        for(int x = 0; x < 200; x++) {
          digitalWrite(stepPin1,HIGH); 
          digitalWrite(stepPin2,HIGH);
          delayMicroseconds(600); 
          digitalWrite(stepPin1,LOW); 
          digitalWrite(stepPin2,LOW); 
          delayMicroseconds(600); 
        }
      delay(890);
      digitalWrite(conveyorPin, LOW); //start conveyor command
      delay(890); //advance tray on conveyor for specified delay
    }
    //determines if tray is not below pot dropper and lowers arm switches
    if(distance >20 && distance <50){
      Servo1.write(0);
      Servo2.write(90);
    }

  }

}

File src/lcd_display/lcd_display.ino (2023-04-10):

// IMPORTANT: Adafruit_TFTLCD LIBRARY MUST BE SPECIFICALLY
// CONFIGURED FOR EITHER THE TFT SHIELD OR THE BREAKOUT BOARD.
// SEE RELEVANT COMMENTS IN Adafruit_TFTLCD.h FOR SETUP.

#include <Adafruit_GFX.h>    // Core graphics library
#include <Adafruit_TFTLCD.h> // Hardware-specific library

// The control pins for the LCD can be assigned to any digital or
// analog pins...but we'll use the analog pins as this allows us to
// double up the pins with the touch screen (see the TFT paint example).
#define LCD_CS A3 // Chip Select goes to Analog 3
#define LCD_CD A2 // Command/Data goes to Analog 2
#define LCD_WR A1 // LCD Write goes to Analog 1
#define LCD_RD A0 // LCD Read goes to Analog 0

#define LCD_RESET A4 // Can alternately just connect to Arduino's reset pin

// When using the BREAKOUT BOARD only, use these 8 data lines to the LCD:
// For the Arduino Uno, Duemilanove, Diecimila, etc.:
//   D0 connects to digital pin 8  (Notice these are
//   D1 connects to digital pin 9   NOT in order!)
//   D2 connects to digital pin 2
//   D3 connects to digital pin 3
//   D4 connects to digital pin 4
//   D5 connects to digital pin 5
//   D6 connects to digital pin 6
//   D7 connects to digital pin 7
// For the Arduino Mega, use digital pins 22 through 29
// (on the 2-row header at the end of the board).

// Assign human-readable names to some common 16-bit color values:
#define	BLACK   0x0000
#define	BLUE    0x001F
#define	RED     0xF800
#define	GREEN   0x07E0
#define CYAN    0x07FF
#define MAGENTA 0xF81F
#define YELLOW  0xFFE0
#define WHITE   0xFFFF

#define BUTTON_X 52
#define BUTTON_Y 150
#define BUTTON_W 80
#define BUTTON_H 45
#define BUTTON_SPACING_X 26
#define BUTTON_SPACING_Y 30
#define BUTTON_TEXTSIZE 3

Adafruit_GFX_Button button[3];


Adafruit_TFTLCD tft(LCD_CS, LCD_CD, LCD_WR, LCD_RD, LCD_RESET);
// If using the shield, all control and data lines are fixed, and
// a simpler declaration can optionally be used:
// Adafruit_TFTLCD tft;

//four status bits for:
// [0] = master switch on/off ie)running
// [1] = missing pot detected
// [2] = refill trays
// [3] = refill pots
byte status[4];
byte state[4] = {0,0,0,0};
byte oldstate[4] = {0,0,0,0};


void setup(void) {
  status[0] = 10;
  status[1] = 11;
  status[2] = 12;
  status[3] = 13;
  pinMode(status[0],INPUT);
  pinMode(status[1],INPUT);
  Serial.begin(9600);
  Serial.println(F("TFT LCD test"));

#ifdef USE_ADAFRUIT_SHIELD_PINOUT
  Serial.println(F("Using Adafruit 2.8\" TFT Arduino Shield Pinout"));
#else
  Serial.println(F("Using Adafruit 2.8\" TFT Breakout Board Pinout"));
#endif

  Serial.print("TFT size is "); Serial.print(tft.width()); Serial.print("x"); Serial.println(tft.height());

  tft.reset();

  uint16_t identifier = tft.readID();

  if(identifier == 0x9325) {
    Serial.println(F("Found ILI9325 LCD driver"));
  } else if(identifier == 0x9328) {
    Serial.println(F("Found ILI9328 LCD driver"));
  } else if(identifier == 0x7575) {
    Serial.println(F("Found HX8347G LCD driver"));
  } else if(identifier == 0x9341) {
    Serial.println(F("Found ILI9341 LCD driver"));
  } else if(identifier == 0x8357) {
    Serial.println(F("Found HX8357D LCD driver"));
  } else {
    Serial.print(F("Unknown LCD driver chip: "));
    Serial.println(identifier, HEX);
    Serial.println(F("If using the Adafruit 2.8\" TFT Arduino shield, the line:"));
    Serial.println(F("  #define USE_ADAFRUIT_SHIELD_PINOUT"));
    Serial.println(F("should appear in the library header (Adafruit_TFT.h)."));
    Serial.println(F("If using the breakout board, it should NOT be #defined!"));
    Serial.println(F("Also if using the breakout, double-check that all wiring"));
    Serial.println(F("matches the tutorial."));
    return;
  }


  
  tft.begin(identifier);
  
  tft.fillScreen(WHITE);
  tft.setRotation(1);
  tft.fillRect(100,0,280,20,BLACK);
  tft.setCursor(160, 2);
  tft.setTextColor(WHITE); 
  tft.setTextSize(2);
  tft.println("Status Monitor");
  
    
  

  

  // button[0].initButton(&tft, 120,117,200,115,BLACK,YELLOW,WHITE,"yep",3);
  // button[0].drawButton();
  masterSwitchOFF();
  verification();
  jam();
  stock();
  

  
  // button[0].initButton(&tft, 120,252,200,115,BLACK,BLUE,WHITE,"blue",3);
  // button[0].drawButton();
    
  }
  



void loop(void) {
  // [0] = master switch on/off ie)running
  // [1] = missing pot detected
  // [2] = refill trays
  // [3] = refill pots
    state[0] = digitalRead(status[0]);
    state[1] = digitalRead(status[1]);
    state[2] = digitalRead(status[2]);
    state[3] = digitalRead(status[3]);

    
    if(state[0]!=oldstate[0]){
      oldstate[0] ^= 1;
      if(state[0]==1){
        masterSwitchON();
      }
      else{
        masterSwitchOFF();
      }
    }

    if(state[1]!=oldstate[1]){
      oldstate[1] ^= 1;
      if(state[1]==1){
        verificationDetected();
      }
      else{
        verification();
      }
    }

    if(state[2]!=oldstate[2]){
      oldstate[2] ^= 1;
      if(state[2]==1){
        jamDetected();
      }
      else{
        jam();
      }
    }

    if(state[3]!=oldstate[3]){
      oldstate[3] ^= 1;
      if(state[3]==1){
        stockDetected();
      }
      else{
        stock();
      }
    }


    
    
  
        
}


void masterSwitchON(){
  tft.fillRoundRect(20,30,215,135,3,GREEN);
  tft.drawRoundRect(20,30,215,135,3,BLACK);
  tft.setCursor(50,35);
  tft.setTextColor(BLACK);
  tft.setTextSize(2);
  tft.print("Master Switch");
  tft.setCursor(90,90);
  tft.setTextColor(BLACK);
  tft.setTextSize(6);
  tft.print("ON");
}
void masterSwitchOFF(){
  tft.fillRoundRect(20,30,215,135,3,RED);
  tft.drawRoundRect(20,30,215,135,3,BLACK);
  tft.setCursor(50,35);
  tft.setTextColor(WHITE);
  tft.setTextSize(2);
  tft.print("Master Switch");
  tft.setCursor(80,90);
  tft.setTextColor(WHITE);
  tft.setTextSize(6);
  tft.print("OFF");
}

void verification(){
  
  tft.fillRoundRect(245,175,215,135,3,GREEN);
  tft.drawRoundRect(245,175,215,135,3,BLACK);
  tft.setCursor(280,180);
  tft.setTextColor(BLACK);
  tft.setTextSize(2);
  tft.print("Verification");
  tft.setCursor(280,235);
  tft.setTextColor(BLACK);
  tft.setTextSize(5);
  tft.print("CLEAR");
}

void verificationDetected(){
  
  tft.fillRoundRect(245,175,215,135,3,YELLOW);
  tft.drawRoundRect(245,175,215,135,3,BLACK);
  tft.setCursor(280,180);
  tft.setTextColor(BLACK);
  tft.setTextSize(2);
  tft.print("Verification");
  tft.setCursor(285,235);
  tft.setTextColor(BLACK);
  tft.setTextSize(3);
  tft.print("WARNING!");
  tft.setCursor(255,265);
  tft.setTextColor(BLACK);
  tft.setTextSize(3);
  tft.print("Pot Missing");
}
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

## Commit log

2022-11-02 traceability table
2022-11-03 Conveyor testing added
2022-11-03 Updated traceability of FR testing
2022-11-03 Updated traceability
2022-11-12 stepper testing
2022-11-14 Added pot dropper and sensor output Arduino code
2023-01-16 motor control testing
2023-01-17 Tray part
    [tray.0001.ipt, tray.ipt]
2023-01-17 tray elevator assembly
    [NEMA 23 84mm Frame Stepper Motor.0001.iam, NEMA 23 84mm Frame Stepper Motor.iam, Tray Elevator.0001.iam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]
2023-01-17 tray elevator update
    [NEMA 23 84mm Frame Stepper Motor_MIR.iam, Tray Elevator.0001.iam, Tray Elevator.0002.iam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]
2023-01-17 parts file structure updated
    [NEMA 23 84mm Frame Stepper Motor.0001.iam, NEMA 23 84mm Frame Stepper Motor.iam, NEMA 23 84mm Frame Stepper Motor_MIR.iam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]
2023-01-18 SysDes hardware and interface updates
    [Armature.ipt, Body020.ipt, Cap.ipt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]
2023-01-18 circuit diagram
2023-01-18 claw design cad
    [claw1.ipt, claw2.ipt, clawbase.ipt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]
2023-01-19 Parts file folder update and sysdes appendix update
    [claw1.ipt, claw2.ipt, clawbase.ipt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]
2023-01-19 MG push
    [pot dropper.ipt, pot dropper.stl]
2023-01-27 Tray dropper parts and assembly
    [1865K21_Easy-Access Base-Mounted Shaft Support.0001.ipt, 1865K21_Easy-Access Base-Mounted Shaft Support.ipt, 5537T012_T-Slotted Framing - 1.5ft.ipt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]
2023-01-28 tray dropper wheel updated design
    [THE_WHEEL 2.0.ipt, THE_WHEEL 2.0.stl]
2023-01-30 tray dropper updates
    [5537T228_T-Slotted Framing - 10in.0001.ipt, 5537T228_T-Slotted Framing - 10in.ipt, Gantry Assembly_new.iam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]
2023-02-02 parts updates
    [THE_WHEEL 2.0.0003.ipt, THE_WHEEL 2.0.0005.ipt, THE_WHEEL 2.0.ipt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]
2023-02-06 conveyor control
2023-03-06 mounting brackets
    [mounting bracket 1.ipt, mounting bracket 1.stl, mounting bracket 2.ipt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]
2023-03-08 trace to requirements
2023-03-08 trace to modules formatting
2023-03-08 trace to modules
2023-03-31 parts, executive summary, logo
    [screen mount.0003.ipt, screen mount.ipt, screen mount.stl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]
2023-03-31 servo code
2023-04-01 verify and conveyor
2023-04-05 SystDes updates
    [Frame 1680721558395.iam, ME4Z03 1680721565852.ipt, ME4Z03 1680721565900.ipt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]
2023-04-05 updated circuit
2023-04-05 made circuit diagram bigger
